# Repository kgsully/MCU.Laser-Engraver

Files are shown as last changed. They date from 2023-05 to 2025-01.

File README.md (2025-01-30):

# Laser Engraver
## **2 Axis laser engraver using the open source FluidNC Firmware**

This repository contains the PCB schematics and layout design as well as STL models for 3D printed components.

Imgur

Imgur

Imgur

Imgur

Imgur

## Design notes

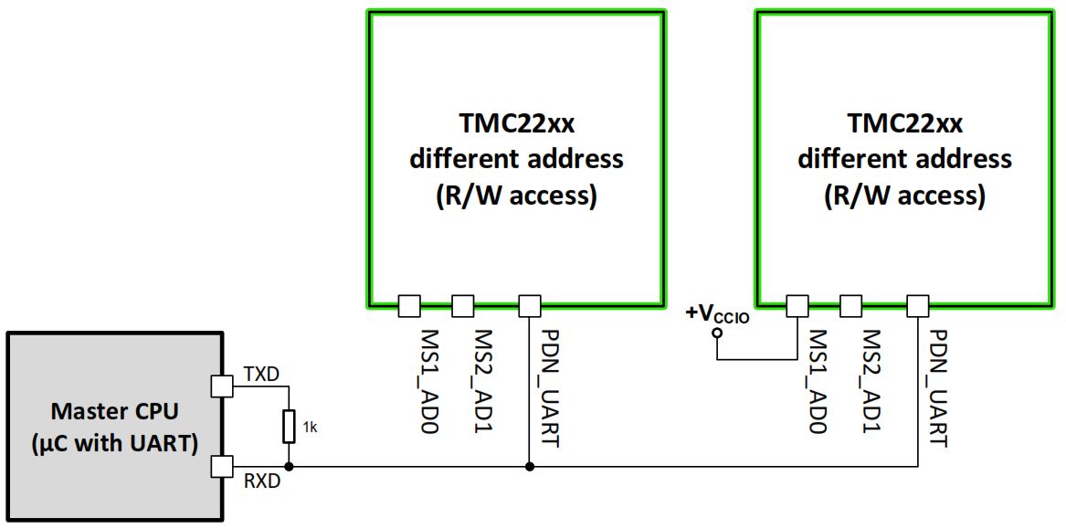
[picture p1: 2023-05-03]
Electrical & PCB/Pictures/TMC2209 - UART.jpg

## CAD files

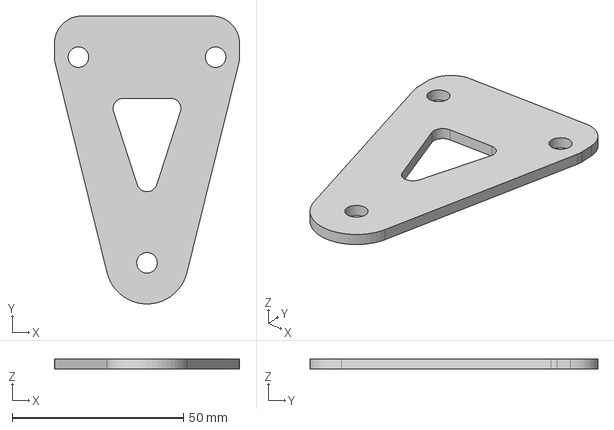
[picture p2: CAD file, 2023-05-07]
Frame & Mechanical/Model/X Axis Support - Inside Support V2.step
54.0 x 84.0 x 3.00 mm

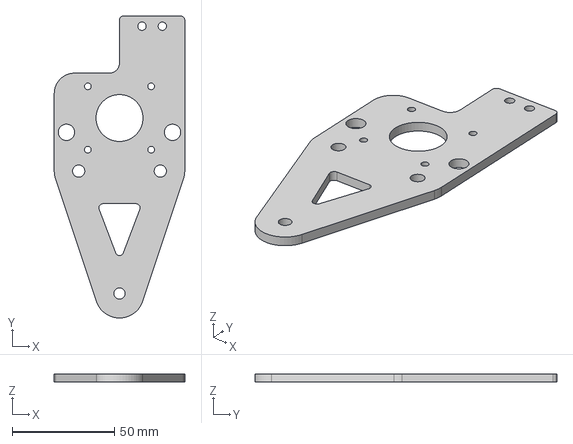
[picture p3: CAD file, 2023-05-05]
Frame & Mechanical/Model/Laser Carriage - Motor Side V2.step
64.0 x 148.0 x 4.00 mm

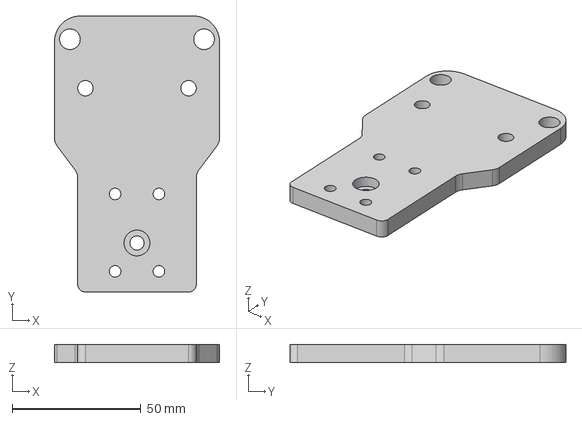
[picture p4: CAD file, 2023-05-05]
Frame & Mechanical/Model/Laser Carriage - Laser Side V2.step
64.0 x 107.0 x 7.00 mm

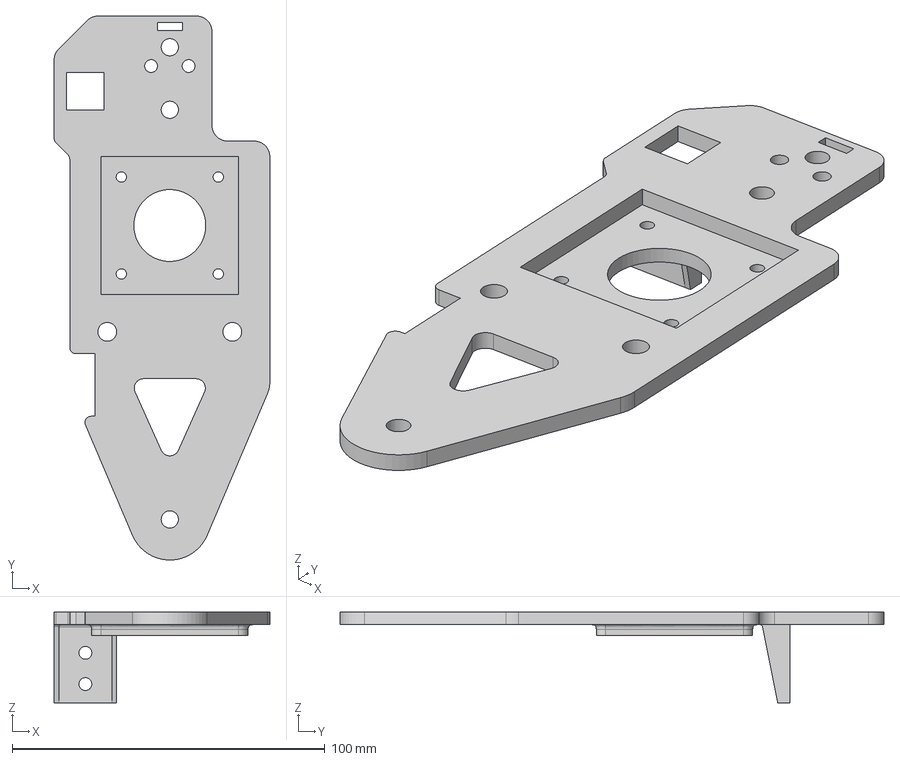
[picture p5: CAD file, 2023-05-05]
Frame & Mechanical/Model/X Axis Support - Motor Side V2.step
69.0 x 174.0 x 29.0 mm

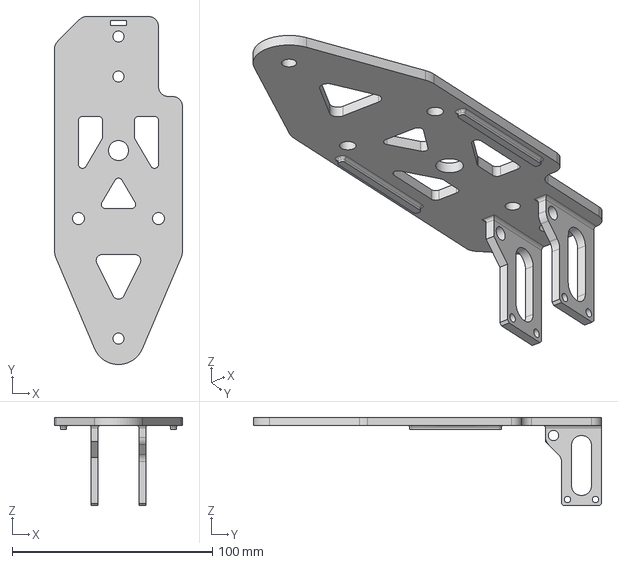
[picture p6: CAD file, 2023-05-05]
Frame & Mechanical/Model/X Axis Support - Passive Side V2.step
64.0 x 174.0 x 44.0 mm

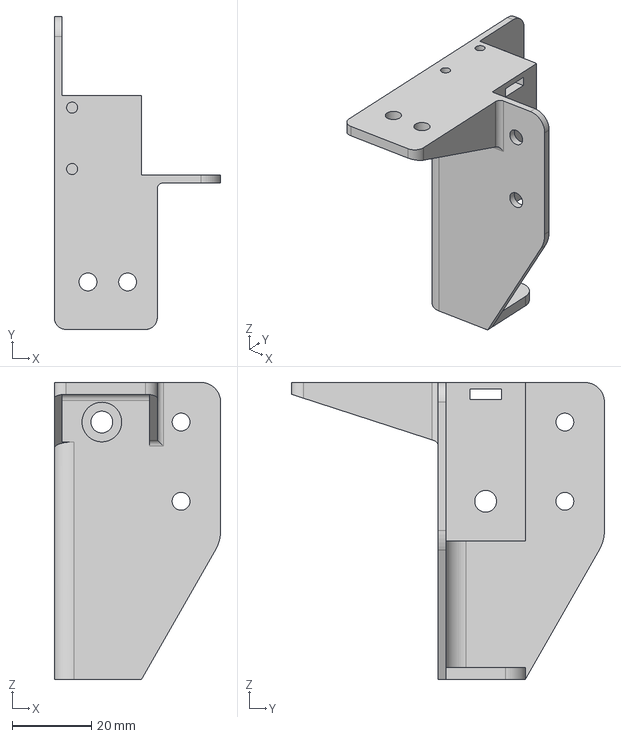
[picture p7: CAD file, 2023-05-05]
Frame & Mechanical/Model/Frame Leg V2 - Rear Left.step
42.0 x 79.0 x 75.0 mm

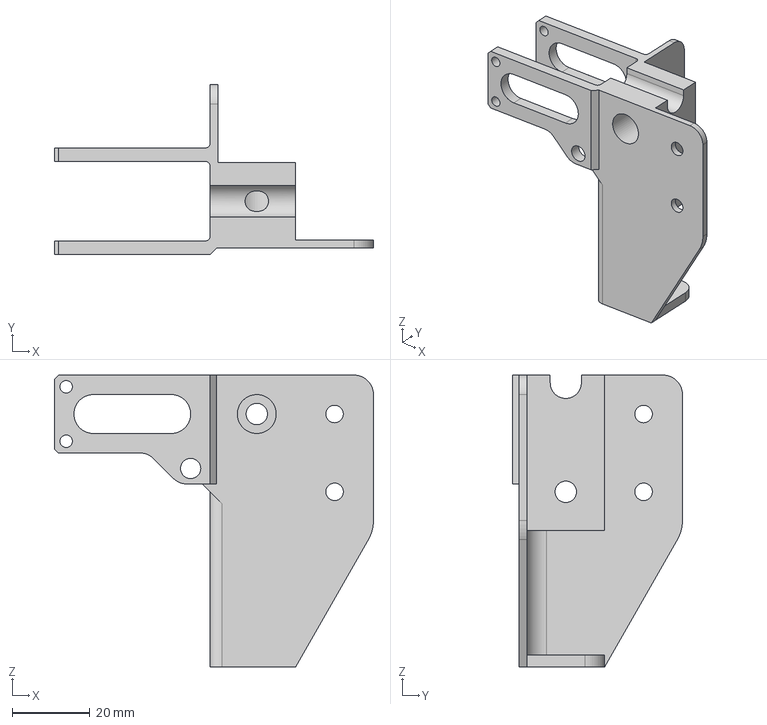
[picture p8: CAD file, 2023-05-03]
Frame & Mechanical/Model/Frame Leg V2 - Front Right.step
82.0 x 43.7 x 75.0 mm

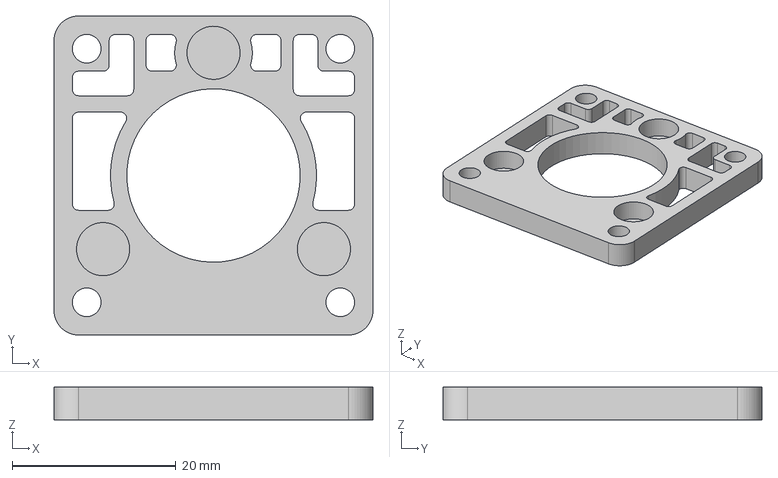
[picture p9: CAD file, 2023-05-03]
Frame & Mechanical/Model/Laser Shroud Magnetic Mount.step
39.0 x 39.0 x 4.00 mm

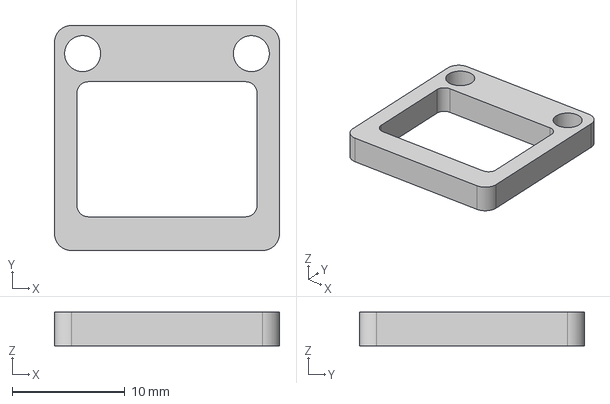
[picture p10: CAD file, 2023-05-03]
Frame & Mechanical/Model/ZSY Standoff.step
20.0 x 20.0 x 3.00 mm

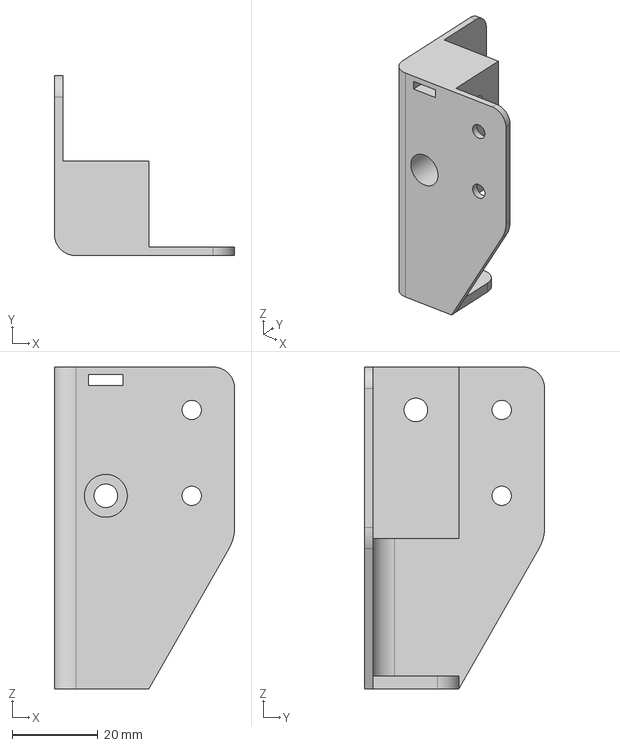
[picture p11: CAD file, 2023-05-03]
Frame & Mechanical/Model/Frame Leg V2 - Rear Right.step
42.0 x 42.0 x 75.0 mm

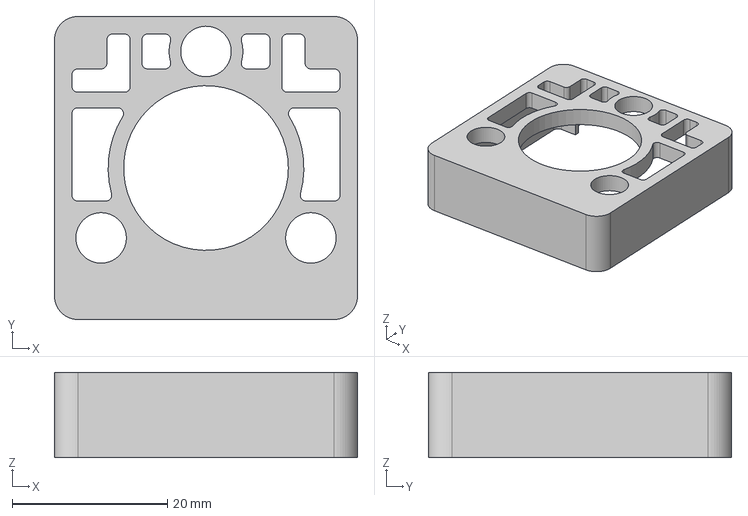
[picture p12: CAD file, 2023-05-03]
Frame & Mechanical/Model/Laser Shroud.step
39.0 x 39.0 x 11.0 mm

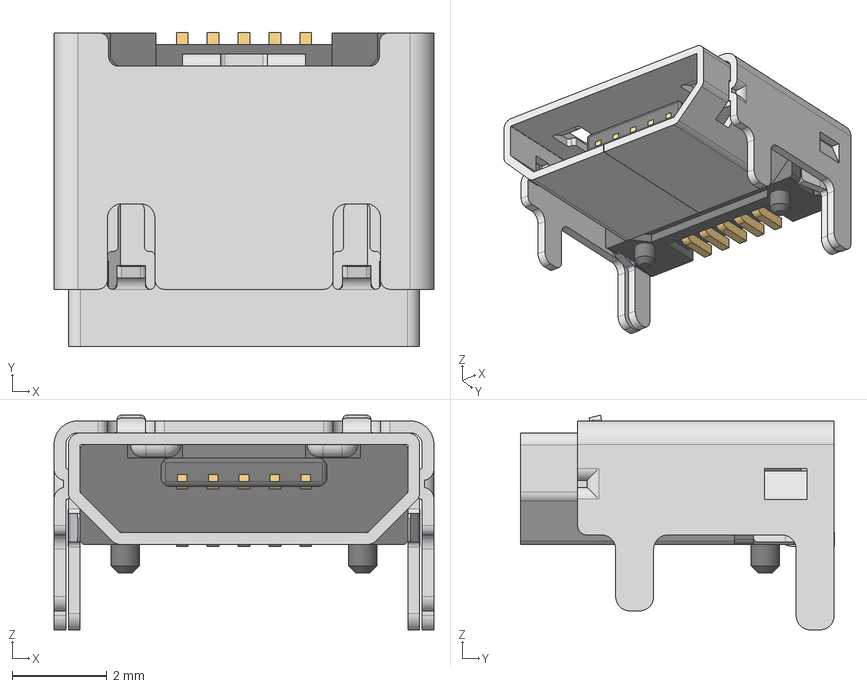
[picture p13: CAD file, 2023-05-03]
Electrical & PCB/Models/629105150521 (rev1).stp
8.00 x 6.60 x 4.52 mm
629105150521_Housing
629105150521_Pin1 x 4
629105150521_Pin2
629105150521_Shielding2
629105150521_Shielding

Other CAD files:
Frame & Mechanical/Model/Frame Leg V2 - Front Left.step
Frame & Mechanical/Model/Frame Leg V2 - Front Left.f3d
Frame & Mechanical/Model/Frame Leg V2 - Front Right.f3d
Frame & Mechanical/Model/Frame Leg V2 - Rear Left.f3d
Frame & Mechanical/Model/Frame Leg V2 - Rear Right.f3d
Frame & Mechanical/Model/Laser Carriage - Laser Side V2.f3d
Frame & Mechanical/Model/Laser Carriage - Motor Side V2.f3d
Frame & Mechanical/Model/Laser Shroud Magnetic Mount.f3d
Frame & Mechanical/Model/Laser Shroud.f3d
Frame & Mechanical/Model/X Axis Support - Inside Support V2.f3d
Frame & Mechanical/Model/X Axis Support - Motor Side V2.f3d
Frame & Mechanical/Model/X Axis Support - Passive Side V2.f3d
Frame & Mechanical/Model/ZSY Standoff.f3d

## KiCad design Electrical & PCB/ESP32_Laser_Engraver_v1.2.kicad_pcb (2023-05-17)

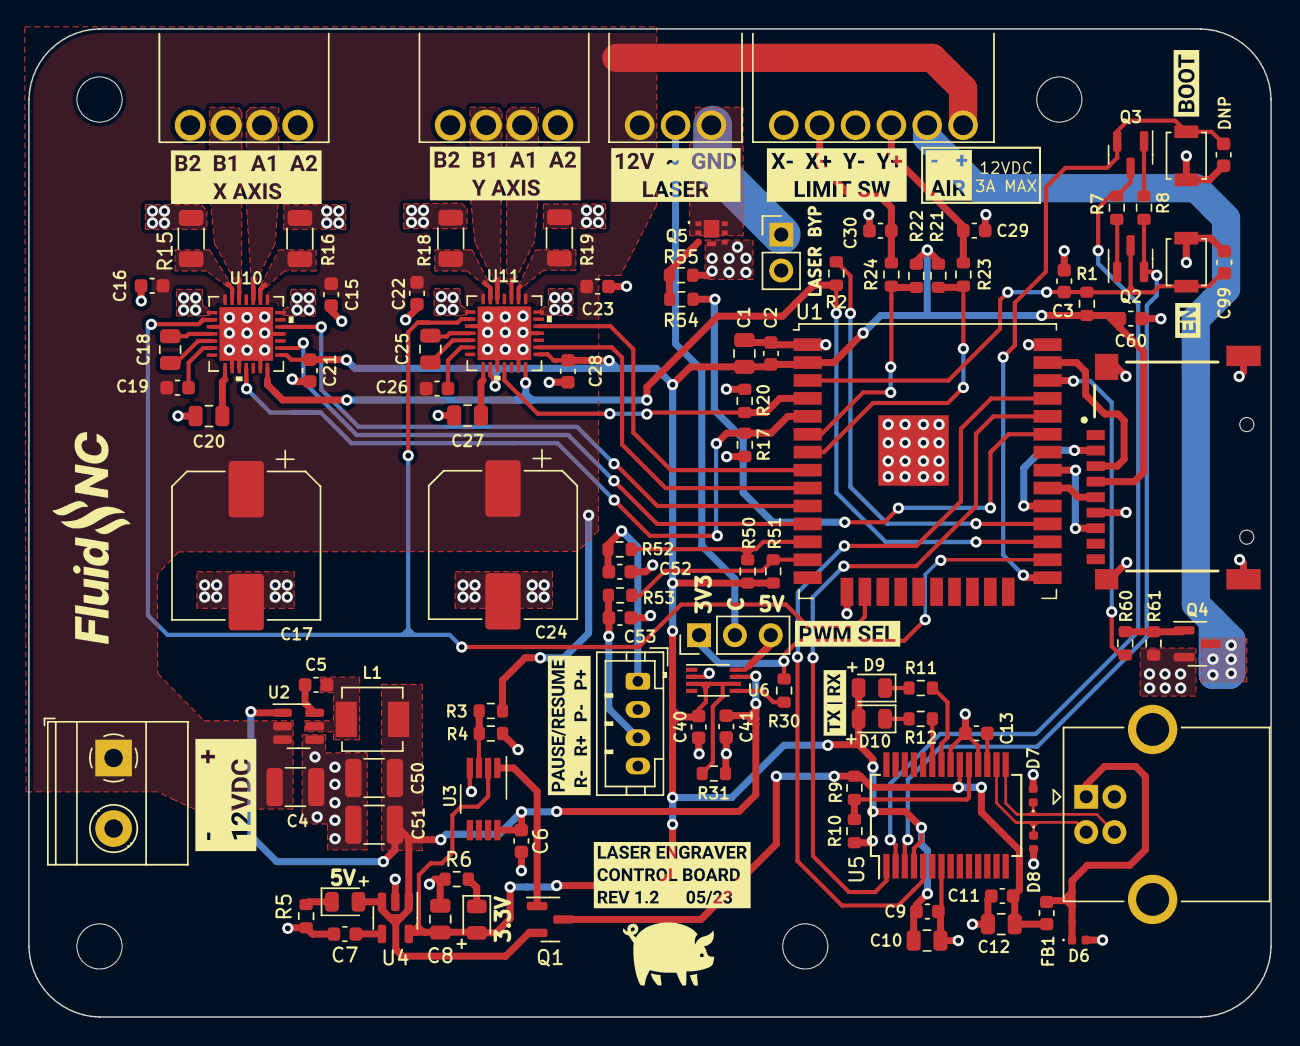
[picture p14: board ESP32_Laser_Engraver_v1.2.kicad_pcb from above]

Board: 2 copper layers, 88.0 x 70.0 mm, 120 parts (0 on the bottom side), 80 nets.

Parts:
C1: 22u; C_0805_2012Metric
C2, C3, C5, C9, C11, C99: 0.1u; C_0603_1608Metric
C4: 10u; C_1210_3225Metric
C6, C15, C16, C19, C21, C22, C23, C26, C28, C29, C30, C40, C41, C52, C53, C60: 100n; C_0603_1608Metric
C7: 10n; C_0603_1608Metric
C8, C20, C27: 2.2u; C_0805_2012Metric
C10, C12: 4.7u; C_0805_2012Metric
C13: 1u; C_0603_1608Metric
C14: 0u; C_0603_1608Metric
C17, C24: 100u; CP_Elec_10x10
C18, C25: 22n; C_0805_2012Metric
C50, C51: 22u; C_1210_3225Metric
D4: RED; LED_0805_2012Metric
D5, D9, D10: GRN; LED_0805_2012Metric
D6, D7, D8: 5VWM; D_0402_1005Metric
FB1: 40R; L_0603_1608Metric
H1, H2, H3, H4: MountingHole; MountingHole_3.2mm_M3
J2: 1935776; TerminalBlock_Phoenix_MKDS-1,5-2_1x02_P5.00mm_Horizontal
J3: USB_B; USB_B_OST_USB-B1HSxx_Horizontal
J10, J11: Screw_Terminal_01x04; KF2EDGR-2.54-4P
J12: Screw_Terminal_01x06; KF2EDGR-2.54-6P
J20: Screw_Terminal_01x03; KF2EDGR-2.54-3P
J21: Conn_01x02_Male; PinHeader_1x02_P2.54mm_Vertical
J22: Conn_01x03_Male; PinHeader_1x03_P2.54mm_Vertical
J100: TF-01A
J101: Conn_01x04_Male; JST_PH_B4B-PH-K_1x04_P2.00mm_Vertical
L1: 4R7; FXL0420-4R7-M
Q1: DMP2110U-7; SOT-23
Q2, Q3: SS8050-G; SOT-23
Q4: SI2302A-TP; SOT-23
Q5: PMPB23XNEZ
R1, R7, R8, R10, R17, R20, R21, R22, R50, R51, R55, R61: 10k; R_0603_1608Metric
R2, R5, R6, R11, R12, R54, R60: 1k; R_0603_1608Metric
R3: 6.8k; R_0603_1608Metric
R4: 4.7k; R_0603_1608Metric
R9: 4k7; R_0603_1608Metric
R15, R16, R18, R19: 0.14R; R_1206_3216Metric
R23, R24, R52, R53: 100R; R_0603_1608Metric
R30: 0R; R_0603_1608Metric
R31: XXXR; R_0603_1608Metric
SW1, SW2: SW_Push; SW_SPST_B3U-1000P
U1: ESP32-WROOM-32U
U2: AP63205WU; TSOT-23-6
U3: LMV358IDGKR; VSSOP-8_3.0x3.0mm_P0.65mm
U4: SPX3819M5-L-3-3; SOT-23-5
U5: CY7C65213-28PVXI; SSOP-28_5.3x10.2mm_P0.65mm
U6: TXS0102DCU; VSSOP-8_2.3x2mm_P0.5mm
U10, U11: TMC2209
kibuzzard-642C7B83: G***; kibuzzard-642C7B83
kibuzzard-642C73EA: G***; kibuzzard-642C73EA
kibuzzard-642C740F: G***; kibuzzard-642C740F
kibuzzard-642DA7F4: G***; kibuzzard-642DA7F4
kibuzzard-642DA8A0: G***; kibuzzard-642DA8A0
kibuzzard-642DA84C: G***; kibuzzard-642DA84C
kibuzzard-642DA806: G***; kibuzzard-642DA806
kibuzzard-6448BA0F: G***; kibuzzard-6448BA0F
kibuzzard-64653C23: G***; kibuzzard-64653C23
kibuzzard-64653D2F: G***; kibuzzard-64653D2F
kibuzzard-6448424C: G***; kibuzzard-6448424C
kibuzzard-64481964: G***; kibuzzard-64481964

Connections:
+3.3V: C1.1, C2.1, C8.1, C9.2, C10.1, C21.1, C28.1, C40.1, C60.1, D5.2 (A), D9.2 (A), D10.2 (A), J100.4 (VDD), R1.1, R21.2, R22.2, R31.1, R50.2, R51.2, U1.2 (VDD), U3.2 (-), U4.5 (OUT), U5.4 (VCCIO), U6.3 (VCCA), U6.6 (OE), U10.15 (VCC_IO), U11.9 (MS1_AD0), U11.15 (VCC_IO)
+5V: C6.1, C41.1, C50.1, C51.1, D4.2 (A), L1.2, Q1.2 (S), U2.1 (FB), U3.8 (V+), U4.1 (IN), U4.3 (EN), U6.7 (VCCB)
/ESP32 MCU/CS_SD: J100.2 (CD/DAT3), U1.29 (IO5)
/ESP32 MCU/DTR: Q3.3 (C), R7.1, U5.2 (DTR)
/ESP32 MCU/EN: C3.1, C99.2, Q2.3 (C), R1.2, SW2.2, U1.3 (EN)
/ESP32 MCU/IO0: C14.2, Q3.2 (E), SW1.2, U1.25 (IO0)
/ESP32 MCU/IO13: U1.16 (IO13), U10.2 (ENN), U11.2 (ENN)
/ESP32 MCU/IO22: R60.1, U1.36 (IO22)
/ESP32 MCU/IO25: U1.10 (IO25), U10.19 (DIR)
/ESP32 MCU/IO26: U1.11 (IO26), U10.16 (STEP)
/ESP32 MCU/IO32: U1.8 (IO32), U11.19 (DIR)
/ESP32 MCU/IO33: U1.9 (IO33), U11.16 (STEP)
/ESP32 MCU/IO34: R22.1, R24.1, U1.6 (IO34)
/ESP32 MCU/IO35: R21.1, R23.1, U1.7 (IO35)
/ESP32 MCU/IO36: R20.2, U1.4 (SENSOR_VP), U11.11 (DIAG)
/ESP32 MCU/IO39: R17.2, U1.5 (SENSOR_VN), U10.11 (DIAG)
/ESP32 MCU/LASER_EN: R54.1, U1.33 (IO21)
/ESP32 MCU/LASER_RET: J20.1, J21.1, Q5.1 (D_1), Q5.2 (D_2), Q5.5 (D_3), Q5.6 (D_4), Q5.7 (D_5)
/ESP32 MCU/MISO: J100.7 (DAT0), U1.31 (IO19)
/ESP32 MCU/MOSI: J100.3 (CMD), U1.37 (IO23)
/ESP32 MCU/PAUSE: R50.1, R52.1, U1.12 (IO27)
/ESP32 MCU/PWM_3V3: J22.1, R30.1, U1.26 (IO4)
/ESP32 MCU/PWM_5V: J22.3, U6.8 (B1)
/ESP32 MCU/RESUME: R51.1, R53.1, U1.13 (IO14)
/ESP32 MCU/RTS: Q2.2 (E), R8.2, U5.3 (RTS)
/ESP32 MCU/RXD: U1.35 (TXD0/IO1), U5.5 (RXD)
/ESP32 MCU/SCK: J100.5 (CLK), U1.30 (IO18)
/ESP32 MCU/TMC_UART: R2.2, U1.27 (IO16), U10.14 (PDN_UART), U11.14 (PDN_UART)
/ESP32 MCU/TXD: U1.34 (RXD0/IO3), U5.1 (TXD)
/Power Supply/5V_SW: C5.2, L1.1, U2.5 (SW)
/Power Supply/VBUS: C11.2, C12.1, FB1.2, Q1.3 (D), R9.2, U5.20 (VCC)
/Stepper Motor Circuits/AIR: J12.2, Q4.3 (D)
/Stepper Motor Circuits/X_BRA: R16.1, U10.23 (BRA)
/Stepper Motor Circuits/X_BRB: R15.1, U10.27 (BRB)
/Stepper Motor Circuits/X_OA1: J10.2, U10.24 (OA1)
/Stepper Motor Circuits/X_OA2: J10.1, U10.21 (OA2)
/Stepper Motor Circuits/X_OB1: J10.3, U10.26 (OB1)
/Stepper Motor Circuits/X_OB2: J10.4, U10.1 (OB2)
/Stepper Motor Circuits/Y_BRA: R19.1, U11.23 (BRA)
/Stepper Motor Circuits/Y_BRB: R18.1, U11.27 (BRB)
/Stepper Motor Circuits/Y_OA1: J11.2, U11.24 (OA1)
/Stepper Motor Circuits/Y_OA2: J11.1, U11.21 (OA2)
/Stepper Motor Circuits/Y_OB1: J11.3, U11.26 (OB1)
/Stepper Motor Circuits/Y_OB2: J11.4, U11.1 (OB2)
/USB-UART Interface/USB_D+: D7.1 (A1), J3.3 (D+), U5.15 (USBDP)
/USB-UART Interface/USB_D-: D8.1 (A1), J3.2 (D-), U5.16 (USBDM)
GND: C1.2, C2.2, C3.2, C4.2, C6.2, C7.2, C8.2, C9.1, C10.2, C11.1, C12.2, C13.2, C14.1, C15.2, C16.2, C17.2, C20.1, C21.2, C22.2, C23.2, C24.2, C27.1, C28.2, C29.2, C30.2, C40.2, C41.2, C50.2, C51.2, C52.2, C53.2, C60.2, C99.1, D6.2 (A2), D7.2 (A2), D8.2 (A2), J2.2, J3.4 (GND), J12.4, J12.6, J21.2, J100.6 (VSS), J100.MP1 (GND), J100.MP2 (GND), J100.MP3 (GND), J100.MP4 (GND), J101.2, J101.4, Q4.2 (S), Q5.4 (S_1), Q5.8 (S_2), R4.2, R5.2, R6.2, R10.1, R15.2, R16.2, R17.1, R18.2, R19.2, R20.1, R31.2, R55.2, R61.2, SW1.1, SW2.1, U1.1 (GND), U1.15 (GND), U1.38 (GND), U1.39 (GND), U2.4 (GND), U3.4 (V-), U4.2 (GND), U5.7 (GND), U5.18 (GND), U5.21 (GND), U6.2 (GND), U10.3 (GND), U10.9 (MS1_AD0), U10.10 (MS2_AD1), U10.13 (CLK), U10.18 (GND), U10.29 (GND), U11.3 (GND), U11.10 (MS2_AD1), U11.13 (CLK), U11.18 (GND), U11.29 (GND)
unnamed: C5.1, U2.6 (BST)
unnamed: C7.1, U4.4 (BP)
unnamed: C13.1, U5.17 (VCCD)
unnamed: C18.1, U10.4 (CPO)
unnamed: C18.2, U10.5 (CPI)
unnamed: C19.2, U10.6 (VCP)
unnamed: C20.2, U10.8 (5VOUT)
unnamed: C25.1, U11.4 (CPO)
unnamed: C25.2, U11.5 (CPI)
unnamed: C26.2, U11.6 (VCP)
unnamed: C27.2, U11.8 (5VOUT)
unnamed: C29.1, J12.3, R23.2
unnamed: C30.1, J12.5, R24.2
unnamed: C52.1, J101.1, R52.2
unnamed: C53.1, J101.3, R53.2
unnamed: D4.1 (K), R5.1
unnamed: D5.1 (K), R6.1
unnamed: D6.1 (A1), FB1.1, J3.1 (VBUS)
unnamed: D9.1 (K), R11.2
unnamed: D10.1 (K), R12.2
unnamed: J20.2, J22.2
unnamed: Q1.1 (G), U3.1
unnamed: Q2.1 (B), R7.2
unnamed: Q3.1 (B), R8.1
unnamed: Q4.1 (G), R60.2, R61.1
unnamed: Q5.3 (G), R54.2, R55.1
unnamed: R2.1, U1.28 (IO17)
unnamed: R3.2, R4.1, U3.3 (+)
unnamed: R9.1, R10.2, U5.19 (~RESET)
unnamed: R11.1, U5.22 (GPIO1)
unnamed: R12.1, U5.23 (GPIO0)
unnamed: R30.2, U6.5 (A1)
VMOT: C4.1, C15.1, C16.1, C17.1, C19.1, C22.1, C23.1, C24.1, C26.1, J2.1, J12.1, J20.3, R3.1, U2.2 (EN), U2.3 (IN), U10.22 (VS), U10.28 (VS), U11.22 (VS), U11.28 (VS)

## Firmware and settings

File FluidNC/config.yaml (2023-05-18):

name: "ChillyPig Laser Engraver"
board: "FluidNC Laser Engraver v1.1"

stepping:
  engine: RMT
  #The following settings are set to the defaults
  idle_ms: 250
  dir_delay_us: 0
  pulse_us: 4
  disable_delay_us: 0

uart1:
  txd_pin: gpio.17
  rxd_pin: gpio.16
  rts_pin: NO_PIN
  cts_pin: NO_PIN
  baud: 115200
  mode: 8N1

axes:
  shared_stepper_disable_pin: gpio.13:high
  
  x:
    steps_per_mm: 180
    max_rate_mm_per_min: 2000
    acceleration_mm_per_sec2: 25
    max_travel_mm: 400
    soft_limits: false
    homing:
      cycle: 2
      positive_direction: false
      mpos_mm: 0.000
      feed_mm_per_min: 100.000
      seek_mm_per_min: 200.000
      settle_ms: 200
      seek_scaler: 1.100
      feed_scaler: 1.100
    
    motor0:
      # External pull-up resistor used for limit switch
      limit_neg_pin: gpio.34:low
      #Diag pin is gpio.39
      tmc_2209:
        uart_num: 1
        addr: 0
        r_sense_ohms: 0.110
        run_amps: 0.100
        hold_amps: 0.500
        microsteps: 32
        stallguard: 0
        stallguard_debug: false
        toff_disable: 0
        toff_stealthchop: 5
        toff_coolstep: 3
        run_mode: StealthChop
        homing_mode: StealthChop
        use_enable: false
        direction_pin: gpio.25
        step_pin: gpio.26
        disable_pin: NO_PIN
    
    motor1:
      null_motor:

  y:
    steps_per_mm: 180
    max_rate_mm_per_min: 2000
    acceleration_mm_per_sec2: 25
    max_travel_mm: 400
    soft_limits: false
    homing:
      cycle: 2
      positive_direction: false
      mpos_mm: 0.000
      feed_mm_per_min: 100.000
      seek_mm_per_min: 200.000
      settle_ms: 200
      seek_scaler: 1.100
      feed_scaler: 1.100

    motor0:
      # External pull-up resistor used for limit switch
      limit_neg_pin: gpio.35:low
      #Diag pin is gpio.36
      tmc_2209:
        uart_num: 1
        addr: 1
        r_sense_ohms: 0.110
        run_amps: 1.500
        hold_amps: 0.500
        microsteps: 32
        stallguard: 0
        stallguard_debug: false
        toff_disable: 0
        toff_stealthchop: 5
        toff_coolstep: 3
        run_mode: StealthChop
        homing_mode: StealthChop
        use_enable: false
        direction_pin: gpio.32
        step_pin: gpio.33
        disable_pin: NO_PIN
    motor1:
      null_motor:

  z:
    steps_per_mm: 100.000
    max_rate_mm_per_min: 1000.000
    acceleration_mm_per_sec2: 100.000
    max_travel_mm: 100.000
    soft_limits: false
    motor0:
      null_motor:
    motor1:
      null_motor:
        
spi:
  miso_pin: gpio.19
  mosi_pin: gpio.23
  sck_pin: gpio.18

sdcard:
  cs_pin: gpio.5
  card_detect_pin: NO_PIN
  frequency_hz: 1000000
  
coolant:
  # Coolant pins are controlled by GCODE M7, M8, & M9. They can be used for other purposes depending on the application.
  # These are included here with the intent to be used for an air assist. Software such as Lightburn can be configured to 
  # issue the GCODE command M8 for air assist. M7 = mist, M8 = Flood, M9 = Off
  mist_pin:  NO_PIN
  flood_pin: gpio.22
 
control:
  # External pull-up resistors used. If no external pull-ups, add :pu suffix to gpio definition
  feed_hold_pin: gpio.27:low:pu
  cycle_start_pin: gpio.14:low:pu
  
Laser:
  pwm_hz: 5000
  output_pin: gpio.4
  enable_pin: gpio.21:pd
  disable_with_s0: false
  s0_with_disable: true
  tool_num: 0
  speed_map: 0=0.000% 1000=100.000%
  off_on_alarm: true

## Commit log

2023-05-03 Initial Commit - VERY WIP
    Initial commit for laser engraver PCB and frame parts design. Very WIP still
    [629105150521 (rev1).stp, ESP32_Laser_Engraver_v1.1.kicad_pcb, ESP32_Laser_Engraver_v1.1.kicad_sch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]
2023-05-05 Mechanical Model Update
    [Frame Leg V2 - Rear Left.f3d, Frame Leg V2 - Rear Left.step, Laser Carriage - Laser Side.f3d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]
2023-05-05 Updated laser carriage models
    [Laser Carriage - Laser Side V2.f3d, Laser Carriage - Laser Side V2.step, Laser Carriage - Motor Side V2.f3d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]
2023-05-07 Inside support CAD model update
    [X Axis Support - Inside Support V2.f3d, X Axis Support - Inside Support V2.step]
2023-05-17 Electrical schematic & PCB layout udpate
    Updated to allow selection / bypass of 3.3V - 5V level converter on laser PWM signal. Laser enable now 3V3 from MCU instead of level converting. This should prevent laser from actuating at power up due to level converter momentarily pulling outputs high at startup.
    [ESP32_Laser_Engraver_v1.1.kicad_pcb, ESP32_Laser_Engraver_v1.2.kicad_pcb, ESP32_Laser_Engraver_v1.2.kicad_sch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]
2023-05-18 Added configuration files
    Added FluidNC configuration and USB-UART Bridge configuration files
    [config.yaml]
